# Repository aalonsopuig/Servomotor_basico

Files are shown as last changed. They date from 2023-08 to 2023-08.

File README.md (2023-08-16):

<html>

<head>
<meta http-equiv="Content-Language" content="es">
<meta name="GENERATOR" content="Microsoft FrontPage 4.0">
<meta name="ProgId" content="FrontPage.Editor.Document">
</head>

<font size="4"><b><i>Diseño de un servomotor controlado
      por bus I<sup>2</sup>C mediante microcontrolador PIC de gama media</i></b></font>
      <p>Por Alejandro Alonso Puig<br>
      Septiembre 2.003<br>
 <hr>
<p align="justify"><br>
En este repositorio podrás encontrar el código software, vídeo e informe técnico
que describe el diseño, tanto desde el punto de vista
electrónico, como informático de un modelo de servomotor basado en microcontrolador PIC16F876, cuya particularidad
consiste en ser controlado por bus I<sup>2</sup>C. Las características principales del
módulo presentado son las siguientes:&nbsp;</p>
<br>
<p align="justify">1. Actúa como Slave permitiendo seleccionar mediante
switches dip la dirección que utilizará en la red I<sup>2</sup>C.&nbsp;</p>
<p align="justify">2. Se puede establecer mediante bus I<sup>2</sup>C tanto la posición
deseada, como el DeadBand&nbsp;</p>
<p align="justify">3. Se puede obtener en todo instante mediante bus I<sup>2</sup>C
el
valor del consumo de corriente del módulo, la temperatura, la posición actual
del eje así como otros ciertos valores de estado&nbsp;</p>
<p align="justify">4. El módulo está protegido para evitar sobrecalentamiento
del mismo mediante sensor de temperatura que activa un mecanismo de ventilación
e incluso la parada del servomotor para evitar daños internos.&nbsp;</p>
<br>
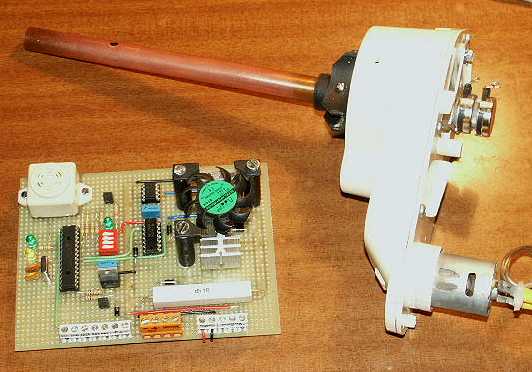
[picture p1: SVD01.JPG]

<p align="justify">La ventaja que se obtiene con este tipo de módulos es
precisamente un control completo por bus I<sup>2</sup>C que hace innecesario tener módulos
específicos para control de servos como ocurre con los de control tipo PWM. De
esta manera pueden controlarse gran cantidad de servos desde un controlador
principal sin apenas sobrecarga en el mismo. Adicionalmente se tienen medida no
habituales, como la de posición real, que permite a nivel de microcontrolador
principal, saber si el servo llegó realmente a su destino o encontró algún
obstáculo que ejercía mayor fuerza que su par. Igualmente la medida de consumo
eléctrico permite conocer cuando el servomotor tiene una sobrecarga de fuerza
contraria a su dirección de movimiento, lo que provoca una subida del consumo
eléctrico medible en este caso.</p>
<br>
<p align="justify">NOTA de 2023: Acabo de subir este proyecto antiguo (de 2003) 
que desarrollé en ensamblador, en mis inicios de aprendizaje de control, por lo que
no aplica un control en bucle cerrado decente, tipo PD o PID.</p>
<br>
<ul>
  <li>
    <p align="justify"><a href="Svd01_docum.pdf">Informe Técnico</a>    <font size="1">(.PDF
    1'9Mb)</font></li>
  <li>
    <p align="justify"><a href="SVD01_04_slave.ASM">Firmware (Programa Slave)</a> <font size="1">(.ASM
    27Kb)</font></li>
  <li>
    <p align="justify"><a href="MSVD04_master.ASM">Programa Master de ejemplo</a> <font size="1">(.ASM
    20Kb)</font></li>
  <li>
    <p align="justify"><a href="SVD01_video.AVI">Video del servo en acción</a><font size="2">
    </font><font size="1">(.AVI 2Mb)</font></li>
</ul>
<br>
<p><b>Nota</b>: Master y Slave han de estar conectados mediante tres hilos:
Masa, SCL y SDA. El módulo presentado incluye las resistencias de PullUp, por
lo que no es necesario añadirlas.&nbsp;</p>
<p>
 
<hr>

</body>

</html>

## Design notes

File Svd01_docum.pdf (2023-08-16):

mundobot.com | Alejandro Alonso Puig

# Diseño de un servomotor controlado por bus I²

C

# mediante un microcontrolador de gama media

# Alejandro Alonso Puig – mundobot.com Septiembre 2003

## Comandos I²

1

mundobot.com | Alejandro Alonso Puig

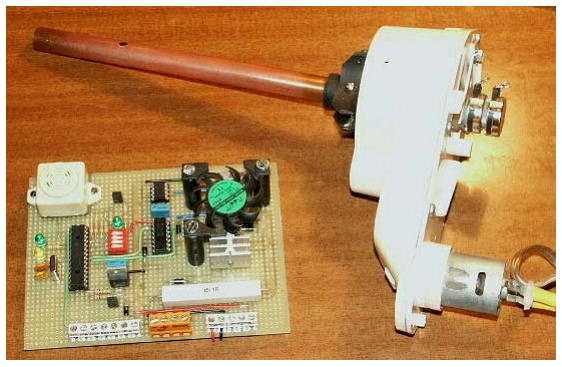
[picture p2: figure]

# Introducción

Este siguiente informe técnico describe el diseño,

## tanto desde el punto de vista electrónico, como informático de un modelo de servomotor cuya particularidad consiste en ser controlado por bus

I

2
C.

## Las características principales del módulo presentado son las siguientes:

## - Actúa como Slave permitiendo seleccionar mediante switches dip la dirección que utilizará en la red I²

C.

## - Se puede establecer mediante bus I²

C

tanto la posición deseada, como el DeadBand - Se puede obtener en todo instante mediante bus I² C el valor del consumo de corriente del módulo, la temperatura, la posición actual del eje así como otros ciertos valores de estado - El módulo está protegido para evitar sobrecalentamiento del mismo mediante sensor de temperatura que activa un mecanismo de ventilación e incluso la parada del servomotor para evitar daños

internos.

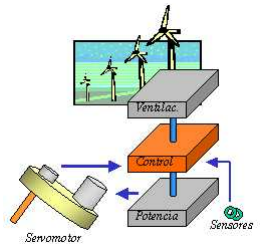
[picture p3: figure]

La ventaja que se obtiene con este tipo de módulos es precisamente un control completo por bus I² C que hace innecesario tener módulos específicos para control de servos como ocurre con los de control tipo PWM. De esta manera pueden controlarse gran cantidad de servos desde un controlador principal sin apenas sobrecarga en el mismo. Adicionalmente se tienen medida no habituales, como la de posición real, que permite a nivel de microcontrolador principal, saber si el servo llegó realmente a su destino o encontró algún obstáculo que ejercía mayor fuerza que su par. Igualmente la medida de consumo eléctrico permite conocer cuando el servomotor tiene una sobrecarga de fuerza contraria a su dirección de movimiento, lo que provoca una subida del

consumo eléctrico medible en este caso.

# Diseño Electrónico

## El módulo está básicamente compuesto por:

## - Servomotor - Sección de control - Sección de potencia para el servomotor - Sección de ventilación - Sensores - Alimentación

2

# Servomotor

## La reductora como es bien sabido permite una reducción de la velocidad de giro del eje a favor

de un aumento del par del mismo.

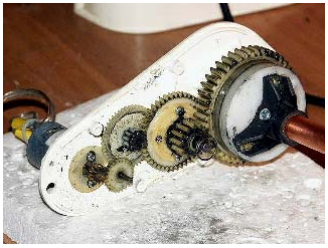
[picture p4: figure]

## En la parte trasera del eje se ha adaptado un potenciómetro lineal de 10KΩ utilizado como divisor de tensión entre 0 y 5v. La salida del

mismo irá a una entrada del microcontrolador,

## configurada para hacer una conversión analógico-digital de 8 bits de resolución, lo que implica que

se | podrán | establecer | 256 | puntos | de
posicionamiento en el servo.

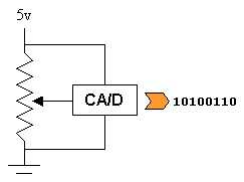
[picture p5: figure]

## El eje de la reductora se ha provisto de topes físicos para evitar que un giro incontrolado pueda

dañar los topes del potenciómetro.

# Sección de control

## La sección de control está basada en un microcontrolador PIC 16F876 de Microchip

funcionando a 4Mhz.

## Este microcontrolador posee un módulo MSSP que permite el control de las comunicaciones I²

C

## por Hardware. Se utilizan los pines SCL (RC3) y SDA (RC4) conectados a resistencias Pull-Up de 1KΩ para las comunicaciones I²

C.

Adicionalmente posee un grupo de conversores analógico digitales (A/D) de los que se utilizarán tres. Uno (RA0/AN0) para la identificación del feedback del potenciómetro, que servirá para obtener la posición del eje del servomotor; otro (RA3/AN3) para convertir la señal analógica lineal (10mV/ºC) proveniente de un sensor de temperatura (LM35), que permitirá prevenir

sobrecalentamientos | del | módulo; | y | otro

## (RA1/AN1) para medir la caída de tensión en una resistencia cementada de 1Ω colocada en serie con la alimentación del módulo de potencia, lo que permitirá identificar el consumo de corriente

del mismo y del servomotor.

## Se utilizan adicionalmente 2 salidas para la

señalización de alarmas por sobrecalentamiento.

Una (RA2) activará la sección de ventilación e indicará su actividad mediante un led. La otra (RA5) se activará solo cuando la actividad del servomotor haya sido detenida por programa debido a un sobrecalentamiento excesivo. Esta salida tiene asociado un led y está conectada a un driver que permite soportar una carga de 2 amperios. Por una parte se le conecta un buzzer de alarma, pero por otra parte se dejan salidas (X3 en esquema) para poder conectarle sistemas adicionales de acción que no superen los 2

amperios mencionados.

## Existen 4 entradas (RB2-RB5) conectadas a un switch-dip cuádruple. Solo las dos inferiores (RB2, RB3) son utilizadas por el firmware actual (versión 4) y permitirán seleccionar diferentes direcciones I² C para evitar coincidencia de

## direccionamiento con otros dispositivos (entre

01111000 [0x78] y 01111110 [0x7E]).

## Dos de las salidas (RB0 y RB1) se utilizarán para el control del servomotor. Para limpiar dichas señales de ruidos indeseados, se han filtrado a través de dobles inversores Schmith Trigger

(74LS14)

## Finalmente los pines MCLR, RB6 y RB7 se han llevado a un conector triple externo (X1 en esquema) con el fin de permitir la programación del chip una vez montado en placa. Un jumper (JP3 en esquema) permite desconectar MCLR de la resistencia de PullUp en el momento de la programación

# Sección de potencia

La sección de potencia permitirá dar al servomotor la corriente que requiere para su funcionamiento. Para ello se han utilizado sendos drivers TC4422 de Microchip que permiten consumos pico de hasta 9 amperios. Dichos drivers están protegidos de las corrientes de autoinducción del motor por un puente de 4

diodos (1N4007).

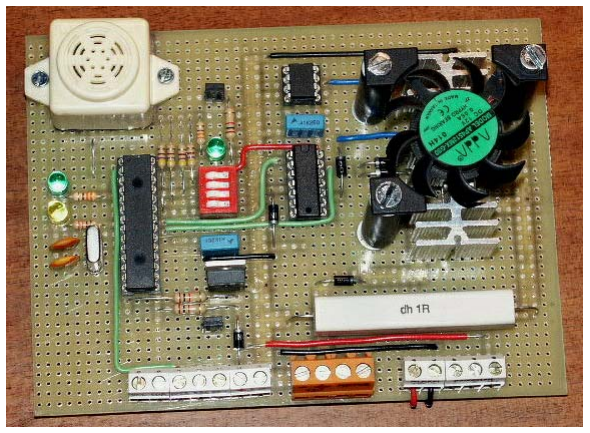
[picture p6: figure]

## Es importante tener en cuenta que la masa utilizada por la sección de potencia es diferente a la masa utilizada por el resto de las secciones. La

## razón es que ambas masas están separadas por la resistencia cementada de 1Ω que nos permite

medir el consumo de corriente del servomotor.

## Por ello existe una pequeña diferencia de potencial correspondiente a la caída de tensión en esta resistencia. Debido a esto y para evitar corrientes inversas de los drivers hacia la sección de control en los flancos de bajada, se utilizan dos

diodos (1N4007) de protección.

# Sección de ventilación

Para proteger el sistema de sobrecalentamientos,

## existe una sección de ventilación activada por la

sección de control.

Básicamente el sistema está formado por un pequeño ventilador y el driver TC4425 de Microchip. Cuando la sección de control identifica que la temperatura ha superado los 46ºC, activa RA2. Su señal es filtrada por una puerta inversora Schmith Trigger y llevada al driver mencionado. Dicho driver activa el

ventilador.

## Una vez que la sección de control considera que la temperatura ha bajado a límites adecuados

(<40ºC), detiene el ventilador.

## Cuando la temperatura sube en exceso (54º), la sección de control detendrá el servomotor, pero la sección de ventilación seguirá activa a la vez que

se activa la alarma.

# Sensores

## El sistema utiliza básicamente dos sensores:

## Sensor de temperatura (LM35): Este sensor produce una variación de potencial en su salida de 10mV por grado centígrado. En la forma en que

## se ha colocado en el circuito, permite un rango de medida de +2ºC hasta 150ºC, aunque existen otras configuraciones que permiten medidas de –55ºC hasta 150ºC (Consultar hoja técnica del fabricante

para más detalles).

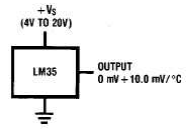
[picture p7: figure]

## Este sensor está unido al radiador de los drivers de potencia del servomotor. Por tanto solo mide la temperatura de dichos drivers y no del servomotor

u otros componentes de la circuitería.

## Sensor de corriente: En realidad no es más que la resistencia de 1Ω que se ha comentado anteriormente. Esta resistencia separa la masa de la sección de potencia y servomotor de la del resto del sistema. Es una resistencia cementada resistente al sobrecalentamiento en caso de alto

consumo de corriente por parte del servomotor.

## Como sabemos por la ley de ohm, la caída de tensión en una resistencia es directamente

proporcional a la corriente que circula por ella. (V=IxR). Si además la resistencia es de 1Ω,

V=Ix1=I, es decir que el valor de caída de potencial es idéntico a la corriente que circula por la resistencia, e igual a la corriente que circula por el servomotor (menos una pequeña corriente consumida en el driver). La realidad es que es difícil una precisión perfecta en las resistencias para que sean de 1Ω exacto, pero en cualquier caso el sistema nos resulta igualmente válido siempre que midamos previamente al montaje el valor de la resistencia y lo consideremos en la fórmula de ohm para un conocimiento exacto de

la corriente circulante.

## La masa de la sección de control y la sección de potencia están separadas por esta resistencia, por lo que la entrada al conversor A/D será

precisamente la masa de la sección de potencia, que variará según la corriente circulante.

## Al utilizar una resistencia de 1Ω, la corriente máxima circulante puede ser de 5 amperios. Si supera este valor se produciría una caída de potencial superior a 5v que al entre en el

conversor A/D podría dañar la sección de control.

## Por eso, aunque el tipo de motor utilizado tiene un consumo de 1 amperio en estado de bloqueo, es conveniente instalar un fusible de 4-5 amperios entre el polo negativo de la fuente de

alimentación y la masa de la circuitería.

## Potenciómetro: Como ya se ha comentado con anterioridad, el potenciómetro es utilizado como divisor de tensión para que permita medir la

posición del eje del servomotor en cada momento.

# Sección de Alimentación

El circuito diseñado permite utilizar dos fuentes de alimentación, de 5v y 12v. La masa de ambas fuentes de alimentación será común para obtener las mismas referencias. La fuente correspondiente a 12v alimentará el servomotor, la sección de potencia y la de ventilación, mientras que la de 5v alimentará la sección de control, el sensor de temperatura y el potenciómetro (divisor de tensión) del servomotor. Es costumbre habitual separar las fuentes de alimentación de las áreas de potencia y control para evitar que las variaciones provocadas por las áreas de potencia afecten a las áreas de control. En cualquier caso este circuito

incluye | la | posibilidad | de | alimentarlo

## exclusivamente con una fuente de alimentación de 12v. Para ello se ha dispuesto un jumper (JP1 en esquema) que permite o no obtener los 5 v necesarios a través de un regulador de tensión 7805. En las pruebas realizadas no se han percibido ruidos de importancia en la circuitería

de control.

## A continuación se muestra un esquema por bloques del sistema descrito. Las líneas de trazado

discontinuo indican las líneas de alimentación.

## Como se observará hay una línea negra más

## gruesa que las demás. Esta indica el otro plano de masas diferente al común y que es utilizado por lo

unidad de potencia.

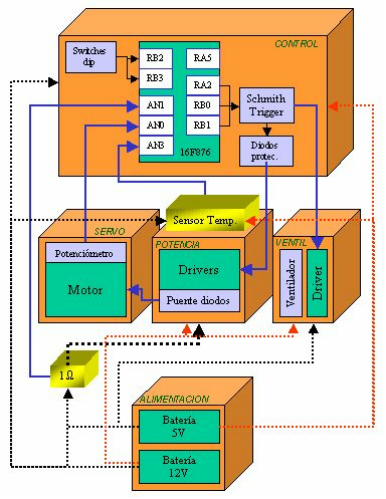
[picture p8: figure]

El esquema eléctrico completo se muestra a continuación.

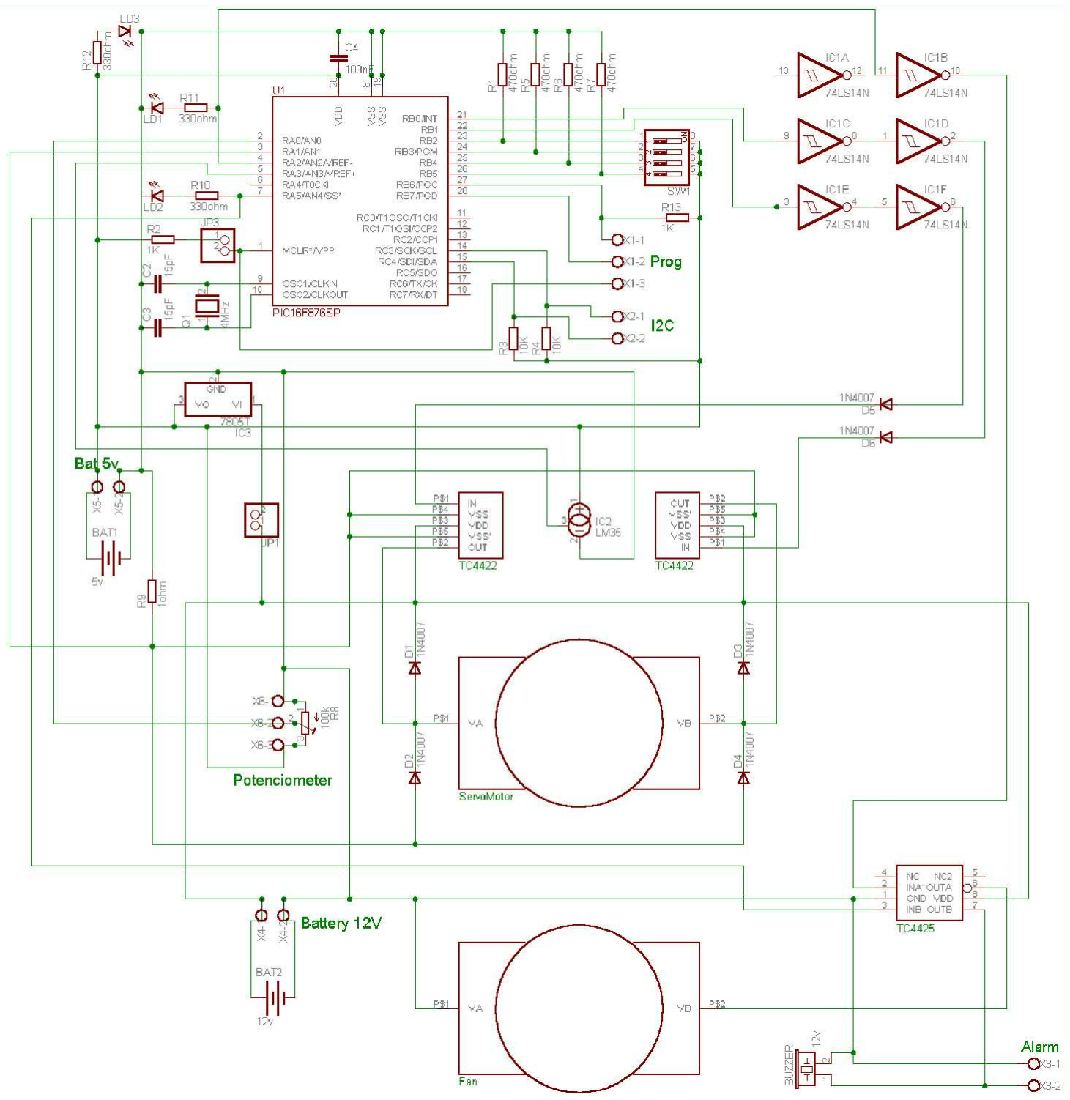
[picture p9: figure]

# Diseño del software

## El software ha sido desarrollado en ensamblador

para PIC16F876.

## El módulo está configurado para producir una interrupción cada vez que se produce un evento

I

2

## C. Al atender dicha interrupción comprueba la información que le llega al microcontrolador y

procede en consecuencia.

# Registros

## El módulo contiene una serie de registros que pueden ser accedidos desde un master por I²

C.
Algunos de estos registros son solo de lectura,

## mientras que otros son de lectura y escritura. Caso especial es uno de los registros, denominado “Estado”, que tiene algunos bits que solo son de lectura y otros que son de lectura/escritura (R/W)

## Mediante el manejo de estos registros se obtiene toda la funcionalidad del módulo. A continuación describimos dichos registros:

## - PosAct y PosNew: En realidad son accedidos desde el master como un único registro. Cuando es accedido en modo escritura, el dato se escribe sobre PosNew y cuando es accedido como lectura, el dato

devuelto es el contenido de PosAct.

## PosNew indica la posición que se desea que tenga el eje del servomotor, mientras que PosAct indica la posición real del eje en el instante en que es accedido el registro. El rango de valores aceptables para el posicionamiento del eje está entre

0+HalfDeadBand+1 y 255-HalfDeadBand-1,

## no obstante, en caso de solicitar una posición fuera de este rango, el programa forzará la posición a los límites indicados

para evitar comportamientos incorrectos.

## Esto implica que en todo momento se podrán seleccionar

### (255-HalfDeadBand-1) - (0+HalfDeadBand+1) +1

es decir,

254-2xHalfDeadBand posiciones.

## La posición por defecto que mantendrá el módulo al arrancar será la que tenga en ese momento, no variándola hasta que le llegue tal orden por I²

C.

- HalfDeadBand: Es un registro R/W.

## Indica la mitad del tamaño de la banda muerta (DeadBand), que es una franja de error aceptable en el posicionamiento del eje del servomotor. Sin esta franja el

servomotor | estaría | constantemente

## tratando de posicionarse en el lugar exacto, impidiéndoselo la inercia del motor. El rango de valores válidos está entre 0 y 255. El valor por defecto que utilizará el módulo si no se le indica otro

será 3.

- Corriente: Es un registro accedido solo en modo lectura. Permite calcular el consumo de corriente de la sección de potencia y servomotor. La medida considerada en realidad en este registro en la caída de potencial en la resistencia de 1Ω mencionada en la sección de Diseño Electrónico. La resolución tomada por el conversor A/D es de 19,5mV/bit. Es decir que por ejemplo, un valor de este registro de 37, implicaría una caída de tensión en

la resistencia de 37x19,5mV= 721,5mV.

## Es importante conocer el valor real de la resistencia si se desea tener valores precisos de consumo. Si la resistencia realmente tiene 1Ω, el consumo será de 721,5mA, pero si el valor real de la resistencia es por ejemplo de 1,5Ω, el valor de consumo de corriente según la ley

## de ohm será I = V/R = 721,5mV/1,5Ω =

481mA

## - Temperatura: Es un registro de solo lectura. Indica la temperatura de la sección de potencia del servomotor. Es utilizada internamente para la activación del sistema de ventilación o bloqueo de la unidad en caso de sobrecalentamiento. La resolución usada en la conversión A/D es

de | 5mV/bit, | que | según | las

## especificaciones del sensor lineal de temperatura utilizado corresponde a 1/2 grado/bit. Ha de tenerse en cuenta adicionalmente que la configuración establecida para el sensor hace que su

rango de valores esté entre 2ºC y 150ºC,

## por lo que una medición de 0v corresponde a 2ºC. Así un valor en este registro de por ejemplo 37 corresponde con un valor en grados centígrados de ºC = (Temperatura/2)+2 = (37/2)+2 = 20,5º

## - Estado: Se trata de un registro especial en el que el bit de mayor peso es R/W y el resto son solo de lectura. Los valores de los bits son los siguientes:

## - Bit 0: Ventilador On/Off. Solo

| lectura.

## - Bit 1: servomotor detenido por

exceso de temperatura On/Off.
| Solo lectura.

## - Bits 2 y 3: Estado posicionamiento servo. Si ambos On, está

| posicionado. | Si | solo | uno

## encendido indica que aún no está

posicionado y el sentido de giro .
| Solo lectura.

## - Bits 4, 5 y 6: No usados - Bit 7: Indica si el servomotor ha sido detenido por orden I² C. Tipo

| R/W
- Versión: Indica la versión del firmware. Es un registro de solo lectura.

# Cuerpo del programa

Básicamente el funcionamiento del programa consiste en un bucle en el que mientras le llega un comando I² C, trata de mantener el eje del servomotor en la posición indicada por “PosNew”, a la vez que actualiza los valores de los demás registros. Inicialmente “PosNew” tendrá el mismo valor que “PosAct”, por lo que si no se le indica por I² C que varíe su posición, se mantendrá de forma activa en la posición que

estaba.

## El chequeo del valor del sensor de temperatura y consiguiente actualización de su registro asociado, se hace junto con un control de márgenes de temperatura según se muestra a continuación:

## - Si el sensor indica un valor de temperatura superior a 46ºC, se activa la sección de ventilación hasta que baje de 40ºC. (RA2 activado). El sistema sigue funcionando

normalmente.

- Si el sensor indica un valor de temperatura superior a 54ºC, se detiene la sección de potencia y por tanto el servomotor hasta que baje de 40ºC. Esto se hace para proteger la unidad de daños críticos. (RA2 y RA5 activados. Este último indica estado de alarma y puede ser utilizado para activar sistemas de aviso). La sección de ventilación y la actualización de los valores de registro sigue activa, así como las funcionalidades del bus I²

C.

# Comandos I²

C

## Básicamente las órdenes que llegarán del Master al Slave serán de lectura y escritura en los registros mencionados anteriormente. En la primera transmisión se indica el número de registro al que se quiere acceder, bien sea para

## lectura o escritura. Dicha numeración es la siguiente:

1. Registro de Estado.
2. No usado.

## 3. Posición. En lectura "PosAct" en escritura "PosNew" 4. Temperatura 5. Corriente 6. HalfDeadBand

7. Revisión Firmware.

## A continuación se muestra el formato de los comandos I² C utilizados para el intercambio de datos entre Master y Slave a nivel de lógica

digital.

## Escritura registro

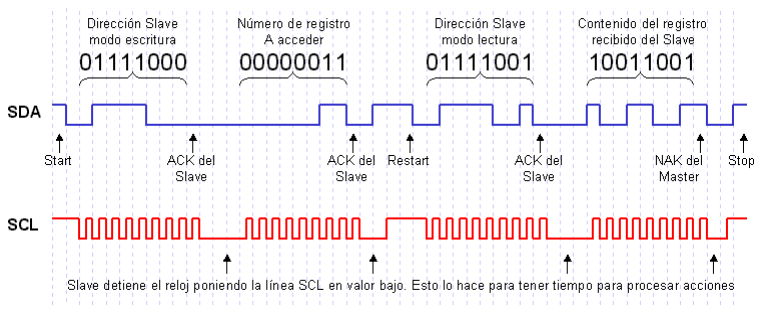
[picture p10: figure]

## El Master envía tres bytes. El primero contiene la dirección del Slave. El segundo, el número de registro a actualizar. El tercero, el dato a escribir

en el registro.

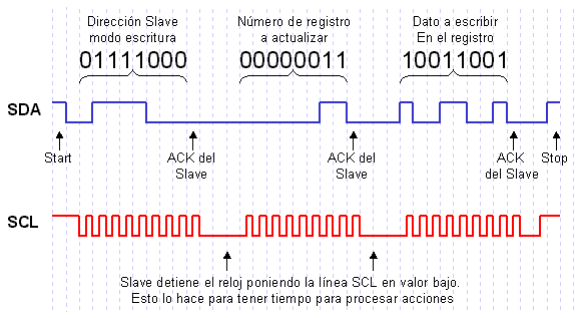
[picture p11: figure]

## Lectura Registro

## Se hacen dos transferencias de dos bytes cada uno. En la primera el Master envía la dirección del Slave y el número de registro a leer. En la segunda transmisión el Master envía la dirección del Slave (pero con bit de lectura) y el Slave envía

el contenido del registro escogido.

# Código fuente

A continuación se incluye el código fuente del servomotor, que actúa tal como se ha comentado en modo Slave.

; SVD01_04
;
; Programa servocontrol (Slave) ; Por: Alejandro Alonso Puig
; Fecha: 10/9/2003
; Controlador: 16F876
; Función:
; Permite control en bucle cerrado de la posición de un motoreductor con ; entrada de feedback por potenciometro. Básicamente es el programa que ; consigue el funcionamiento como servomotor.
; La comunicación con el exterior se hace mediante bus I2C.
; Adicionalmente se mide el consumo de corriente y temperatura
; Tiene medidas de autoprotección con activación de una señal para ventilación ; en caso de superar una temperatura dada y parada de servomotor en caso de
; superar una temperatura límite.
; Shitches dip para especificar la dirección i2c que se utilizará

list | p=16F876
include | "P16F876.INC"

;Definición de macros

#define Ventilador | PORTA,2 ;Bit de activación de ventilador

#define AlarmaTemp | PORTA,5 ;Bit de activación de alarma. El módulo se detiene

| | ;por exceso de temperatura.
#define Version | d'04' | ;Versión del programa

;Definición de variables

cblock 0x20

HalfDeadBand ;valor de mitad de banda de precisión de posicionamiento ;cuanto menor sea, más precisa es la posición ;DeadBand=2*HalfDeadBand
PosAct | ;Posición actual del servo según Potenciómetro (0 a 255)
PosNew | ;Posicion deseada del servo (0+HalfDeadBand+1 a 255-HalfDeadBand-1)
PosNewL | ;PosNewL y PosNewH son los extremos inferior y superior..
PosNewH | ;..a PosNew para establecer el margen según "DeadBand"
PosMax | ;Valores máximo y mínimo que se puede dar a "PosAct"...
PosMin | ;..en función del HalfDeadBand. Básicamente son..
;(0+HalfDeadBand+1 a 255-HalfDeadBand-1)
Corriente | ;Consumo de corriente del módulo (ver proc ChkCurrent)
Temperatura | ;Temperatura del módulo de potencia (ver proc ChkTemperatura)
Estado | ;Registro especial de estado del módulo
; | Bit0: Ventilador On/Off
; | Bit1: servomotor detenido por exceso de temperatura On/Off
; | Bits2 y 3: Estado posicionamiento servo. Si ambos On, está
; | posicionado. Si solo uno encendido indica que aún
; | no está posicionado y el sentido de giro.
; | Bit7: Indica si el servomotor ha sido detenido por orden i2c
DirNodo | ;Dirección I2C de este slave (4 posibles direcciones segun switches dip)
MensajeIn | ;Contendrá el dato recibido por I2C del master
MensajeOut | ;Contendrá el dato a enviar por I2C al master
BkStatus | ;Backup del registro STATUS
BkW | ;Backup W
Temp | ;Variable Temporal usada para evaluación de eventos I2C
Registro | ;Registro accedido por i2c:
; | 1: Registro de Estado. Variable "Estado"
; | 2: No usado. Reservado para velocidad en proximas versiones
; | 3: Posición. En lectura "PosAct" en escritura "PosNew"
; | 4: Temperatura
; | 5: Corriente
; | 6: HalfDeadBand
; | 7: Revisión Firmware. "Version"
StatI2C | ;Registro intermedio para identificar el estado i2c:
; | 0: Si On --> llegó dato Registro (por tanto si llega llega otro
; | dato, será para sobreescribir contenido registro dado)
BDel0 | ;Usada en retardos
BDel1 | ;Usada en retardos
BDel2 | ;Usada en retardos
Pausa | ;Usada para hacer pausas con subr "HacerTiempo"
endc | ;Fin de definiciones
org | 0
goto | INICIO
org | 5

;-------------------------------------------------------------------------------
Interrupcion | ;RUTINA DE INTERRUPCIÓN. Se ocupa de los eventos I2C
;-------------------------------------------------------------------------------

;Guardamos copia de algunos registros

movwf | BkW | ;Hace copia de W
movf | STATUS,W | ;Hace copia de registro de estado
banksel PORTA
movwf BkStatus

;Chequeamos si la interrupción es por evento I2C. En caso positivo llamamos ;a la rutina de proceso del evento
banksel PIR1
btfss | PIR1,SSPIF | ;Ha ocurrido un evento SSP? (I2C)
goto | IntNoSSP | ;No. entonces será por otra cosa. Saltamos.
call | SSP_Handler | ;Si. Procesamos el evento. Si se reciben ordenes, quedarán
| | ;registradas en "MensajeIn". Se enviarán las ordenes
| | ;guardadas en "MensajeOut".
banksel PIR1
bcf | PIR1,SSPIF | ;Limpiamos el flag
goto | Rest
IntNoSSP | ;Aquí se gestionan interrupciones que no son por SSP
; |
; En caso de necesitarse, poner aquí la rutina de gestión de interrupciones ; que no sean por bus I2C
; |
Rest | ;Restauramos las copias de los registros
movf | BkStatus,W | ;Restaura las copias de registros
movwf | STATUS | ;registro de estado
movf | BkW,W | ;registro W

retfie

;-------------------------------------------------------------------------------

INICIO | ;Inicio del cuerpo del programa
banksel TRISB | ;Apunta a banco 1
movlw | b'00111100' | ;Salida excepto B2, B3, B4 y B5 que tiene switches dip
movwf | TRISB | ;

;Configuración para uso de conversor A/D
banksel ADCON1
movlw | b'00001011' | ;Establece puerta A como salida excepto RA0 ...
movwf | TRISA | ;..(Potenciómetro), RA1 (medición corriente) y RA3 (Temperatura)
movlw | b'00000100' | ;PORTA: RA0, RA1, RA3 entrada analog. Resto dig. Justif ADRESH
movwf | ADCON1 | ;

;Inicialización variable de posición del servomotor
banksel PosAct
call | ChkPosAct | ;Identificación posición actual del servo..
movf | PosAct,W | ;..y la guardamos en PosNew..
movwf | PosNew | ;..para que el servo no se mueva...

;Establecemos valor de DeadBand por defecto. Se puede modificar por i2c
movlw | d'3'
movwf | HalfDeadBand

;Establecemos valor registro especial de estado por defecto
movlw | b'10000000'
movwf | Estado

;Configuración para gestión i2c
call init_i2c_Slave ;Configuración para uso de i2c banksel INTCON
bsf | INTCON,GIE | ;Activamos las interrupciones

banksel PORTA
clrf | PORTA
clrf | PORTB
clrf | StatI2C

BUCLE | ;Bucle principal del programa
StSt | ;Chequeo bit de start/stop del servomotor en registro especial de estado
btfsc | Estado,7 | ;On:servomotor funciona, Off:servomotor se detiene
goto | StON | ;Está On. Seguimos
call | PararMotor | ;Está Off. Paramos servomotor,...
call | ChkPosAct | ;..pero seguimos midiendo variables...
call | ChkCurrent | ;..por si son solicitadas por i2c
call | ChkTemperatura ;Además el ventilador seguira activo si es necesario
goto | StSt | ;y nos mantenemos en bucle hasta que se active por i2c

StON

;Chequeo Temperatura
call ChkTemperatura

;Chequeo de consumo eléctrico
call ChkCurrent

;Verificamos valor de PosNew para que no sobrepase los límites: ;(0+HalfDeadBand+1 a 255-HalfDeadBand-1)
;Si PosNew > 255-HalfDeadBand-1 then PosNew=255-HalfDeadBand-1 ;Si PosNew < HalfDeadBand+1 then PosNew=HalfDeadBand+1
movf | HalfDeadBand,W
addlw | d'1'
movwf | PosMin | ;0+HalfDeadBand+1
movlw | d'254'
movwf | PosMax
movf | HalfDeadBand,W
subwf | PosMax,F | ;255-HalfDeadBand-1

;Checkea si PosNew > PosMax
movf | PosMax,W | ;
subwf | PosNew,W | ;Resta/compara con "PosNew"
btfsc | STATUS,Z | ;Son iguales (Z=1)??
goto | OkSigue | ;Si. Está en el límite de posición, pero es correcto
btfsc | STATUS,C | ;No. Mayor (C=0)??
goto | FuerzaMax | ;Si. (PosNew > PosMax) Forzamos que no pase del límite
goto | ChkMenos | ;No, (PosNew < PosMax)
ChkMenos | ;Checkea si PosNew < PosMin
movf | PosMin,W | ;
subwf | PosNew,W | ;Resta/compara con "PosNew"
btfsc | STATUS,Z | ;Son iguales (Z=1)??
goto | OkSigue | ;Si. Está en el límite de posición, pero es correcto
btfsc | STATUS,C | ;No. Mayor (C=0)??
goto | OkSigue | ;Si. (PosNew > PosMin) está ok: PosMin<PosNew<PosMax
goto | FuerzaMin | ;No, (PosNew < PosMin) Forzamos que no pase del límite
FuerzaMax | ;Fuerza a que la posición no pase del máximo
movf | PosMax,w
movwf | PosNew
goto | OkSigue
FuerzaMin | ;Fuerza a que la posición no pase del mínimo
movf | PosMin,W
movwf | PosNew
goto | OkSigue

OkSigue

;Cálculo PosNewH y PosNewL en función del valor de PosNew
movf | PosNew,W
movwf | PosNewH
movwf | PosNewL
movf | HalfDeadBand,W
addwf | PosNewH,F
subwf | PosNewL,F

;Identificación posición actual del servo
call | ChkPosAct
ChkMayor | ;Checkea si PosAct > PosNewH --> Giro antihorario
movf | PosNewH,W | ;
subwf | PosAct,W | ;Resta/compara con "PosAct"

btfsc | STATUS,Z | ;Son iguales (Z=1)??
goto | OkPosic | ;Si. Está en el límite de DeadBand pero se da por bueno
btfsc | STATUS,C | ;No. Mayor (C=0)??
goto | GiroAntihora | ;Si. (PosAct > PosNewH) Activamos motor
goto | ChkMenor | ;No, (PosAct < PosNewH)
ChkMenor | ;Checkea si PosAct < PosNewL --> Giro antihorario
movf | PosNewL,W | ;
subwf | PosAct,W | ;Resta/compara con "PosAct"
btfsc | STATUS,Z | ;Son iguales (Z=1)??
goto | OkPosic | ;Si. Está en el límite de DeadBand pero se da por bueno
btfsc | STATUS,C | ;No. Mayor (C=0)??
goto | OkPosic | ;Si. (PosAct > PosNewL) está en Deadband:PosNewL< PosAct < PosNewH
goto | GiroHora | ;No, (PosAct < PosNewL) Activamos motor
OkPosic | ;Paramos motor
call | PararMotor
goto | BUCLE
GiroHora | ;Activamos motor sentido Horario y actualizamos valor registro especial Estado
bsf | PORTB,0
bcf | PORTB,1
bsf | Estado,2
bcf | Estado,3
goto | BUCLE
GiroAntihora | ;Activamos motor sentido Antihorario y actualizamos valor registro especial Estado
bcf | PORTB,0
bsf | PORTB,1
bcf | Estado,2
bsf | Estado,3
goto | BUCLE
goto | BUCLE

;********************************************************************************* ; SUBRUTINAS
;*********************************************************************************

;-------------------------------------------------------------------------------
ChkPosAct | ;Identifica la posición actual del servo mediante la
;la conversión A/D del valor dado por el potenciómetro ;y lo deja en la variable "PosAct" ;-------------------------------------------------------------------------------

;Tomaremos datos de ADRESH
banksel ADCON1
bcf ADCON1,ADFM

banksel ADCON0
movlw | b'11000001' | ;PORTA-RA0: osci interno, canal-0, activar captura
movwf | ADCON0 | ;
movlw | d'1' | ;Pausa para que de tiempo al condensador interno...
movwf | Pausa | ;..a capturar el valor analógico
call | HacerTiempo
bsf | ADCON0,GO | ;Comenzar conversión A/D
AD_W1 | btfsc | ADCON0,GO_DONE ;Conversión finalizada?
goto | AD_W1
movf | ADRESH,W
movwf | PosAct | ;Guarda en variable de posición actual
return

;-------------------------------------------------------------------------------
ChkCurrent | ;Obtiene el consumo de corriente del módulo servomotor
;mediante conversión A/D de la caida de potencial de una ;resistencia de 1 ohm. El valor obtenido se almacena en la ;variable "Corriente" de manera que el consumo en amperios

;se puede calcular con la fórmula siguiente:
; | Amperios=(Corriente x 0.02)/R
;siendo R la resistencia de medición, que en principio es de ;1ohm, pero que conviene medir para que los calculos sean exactos ;La máxima corriente que puede medir es 255x0.02=5.1 amperios ;Si la corriente va a ser superior, habra que reducir el valor ;de la resistencia de manera que Max Amperios x R < 5 ;-------------------------------------------------------------------------------

;Tomaremos datos de ADRESH
banksel ADCON1
bcf ADCON1,ADFM

banksel ADCON0
movlw | b'11001001' | ;PORTA-RA1: osci interno, canal-1, activar conversion
movwf | ADCON0 | ;
movlw | d'1' | ;Pausa para que de tiempo al condensador interno...
movwf | Pausa | ;..a capturar el valor analógico
call | HacerTiempo
bsf | ADCON0,GO | ;Comenzar conversión A/D
AD_W2 | btfsc | ADCON0,GO_DONE ;Conversión finalizada?
goto | AD_W2
movf | ADRESH,W
movwf | Corriente | ;Guarda en variable de medición de corriente
return

;-------------------------------------------------------------------------------
ChkTemperatura | ;Obtiene la temperatura del módulo de potencia del servomotor
;mediante conversión A/D de la salida del sensor LM35 ;y la almacena en la variable "Temperatura"
;La temperatura en ºC del módulo será igual a:
; | ºC=(Temperatura/2)+2
;-------------------------------------------------------------------------------

;Tomaremos datos de ADRESL para tener una precisión de medio grado por bit banksel ADCON1
bsf ADCON1,ADFM

banksel ADCON0
movlw | b'11011001' | ;PORTA-RA3: osci interno, canal-3, activar conversion
movwf | ADCON0 | ;
movlw | d'1' | ;Pausa para que de tiempo al condensador interno...
movwf | Pausa | ;..a capturar el valor analógico
call | HacerTiempo
bsf | ADCON0,GO | ;Comenzar conversión A/D
AD_W3 | btfsc | ADCON0,GO_DONE ;Conversión finalizada?
goto | AD_W3
banksel ADRESL
movf ADRESL,W
banksel Temperatura
movwf | Temperatura | ;Guarda en variable de medición de temperatura

;Los drivers utilizados tienen un rango de funcionamiento entre 0º y 70ºC ;Checkeamos si ha superado 46ºC, con lo que activaríamos ventilador hasta ;que baje de 40ºC
movlw | d'88' | ;46ºC=factor 88 --->(88/2)+2=46
subwf | Temperatura,W ;Resta/compara con "Temperatura"
btfsc | STATUS,Z | ;Son iguales (Z=1)??
goto | VentiladorOn | ;Si. Activamos ventilador
btfsc | STATUS,C | ;No. Mayor (C=0)??
goto | VentiladorOn | ;Si. Límite de temperatura superado
;No, verificamos si menor que 40º
movlw | d'76' | ;40ºC=factor 76 --->(76/2)+2=40
subwf | Temperatura,W ;Resta/compara con "Temperatura"
btfsc | STATUS,Z | ;Son iguales (Z=1)??
goto | FinChk | ;Si. no hacemos nada. Si ventilador activado, continuará así
btfsc | STATUS,C | ;No. Mayor (C=0)??
goto | FinChk | ;Si. no hacemos nada. Si ventilador activado, continuará así
goto | VentiladorOff ;No, ha bajado de 40º, podemos desactivar ventilador

VentiladorOn

bsf | Ventilador | ;Activamos ventilador
bsf | Estado,0 | ;..y registro especial de estado

;Checkeamos si ha superado 54ºC, con lo que detendríamos el módulo ;para evitar sobrecalentamiento hasta que baje de 40ºC
movlw | d'104' | ;54ºC=factor 104 --->(104/2)+2=54
subwf | Temperatura,W ;Resta/compara con "Temperatura"
btfsc | STATUS,Z | ;Son iguales (Z=1)??
goto | AlarmOn | ;Si. Activamos procedimiento de alarma por sobrecalentamiento
btfsc | STATUS,C | ;No. Mayor (C=0)??
goto | AlarmOn | ;Si. Límite de temperatura superado
;No, todo en orden
goto FinChk

VentiladorOff
bcf | Ventilador | ;Paramos ventilador
bcf | Estado,0 | ;..y registro especial de estado
goto | FinChk

AlarmOn ;Procedimiento ante sobrecalentamiento del módulo

;Paramos motor
call PararMotor

;Activamos bit de alarma por sobrecalentamiento
bsf | AlarmaTemp
bsf | Estado,1 | ;..y registro especial de estado
ChkT | ;Entramos en bucle hasta que baje de 40ºC
banksel ADCON0
movlw | b'11011001' | ;PORTA-RA3: osci interno, canal-3, activar conversion
movwf | ADCON0 | ;
movlw | d'1' | ;Pausa para que de tiempo al condensador interno...
movwf | Pausa | ;..a capturar el valor analógico
call | HacerTiempo
bsf | ADCON0,GO | ;Comenzar conversión A/D
AD_W4 | btfsc | ADCON0,GO_DONE ;Conversión finalizada?
goto | AD_W4
banksel ADRESL
movf ADRESL,W
banksel Temperatura
movwf | Temperatura | ;Guarda en variable de medición de temperatura
movlw | d'76' | ;40ºC=factor 76 --->(76/2)+2=40
subwf | Temperatura,W ;Resta/compara con "Temperatura"
btfsc | STATUS,Z | ;Son iguales (Z=1)??
goto | ChkT | ;Si. continuamos en bucle hasta que se enfrie
btfsc | STATUS,C | ;No. Mayor (C=0)??
goto | ChkT | ;Si. continuamos en bucle hasta que se enfrie
bcf | AlarmaTemp | ;No, ha bajado de 40º, podemos desactivar condicion alarma
bcf | Ventilador | ;Paramos ventilador
bcf | Estado,0 | ;..y registro especial de estado
goto | FinChk

FinChk
return

;-------------------------------------------------------------------------------
PararMotor | ;Detiene el servomotor
;-------------------------------------------------------------------------------
bsf | PORTB,0
bsf | PORTB,1
bsf | Estado,2
bsf | Estado,3
return

;-------------------------------------------------------------------------------
init_i2c_Slave | ;Inicializa valores para uso de I2C en Slave ;Ha de ser llamado tras definir TRISC (de ser necesario)

;-------------------------------------------------------------------------------

;Guardamos copia de algunos registros
movwf | BkW | ;Hace copia de W
movf | STATUS,W | ;Hace copia de registro de estado
banksel PORTA
movwf BkStatus

;Establecemos dirección del esclavo segun switches dip (B2 y B3)
movlw | b'01111000'
movwf | DirNodo
btfsc | PORTB,2
bsf | DirNodo,2
btfsc | PORTB,3
bsf | DirNodo,1

;Configuramos I2C
banksel TRISC | ; Pasamos a direccionar Banco 1
movlw | b'00011000' | ; Establece líneas SDA y SCL como entradas...
iorwf | TRISC,F | ;..respetando los valores para otras líneas.
bcf | SSPSTAT,CKE | ; Establece I2C input levels
bcf | SSPSTAT,SMP | ; Habilita slew rate
bsf | SSPCON2,GCEN | ; Habilita direccionamiento global
banksel DirNodo
movf | DirNodo,W | ; Dirección esclavo
banksel SSPADD
movwf | SSPADD | ;
banksel SSPCON | ; Pasamos a direccionar Banco 0
movlw | b'00110110' | ; Slave mode, SSP enable,
movwf | SSPCON | ;
bcf | PIR1,SSPIF | ; Limpia flag de eventos SSP
bcf | PIR1,7 | ; Limpia bit. Mandatorio por Datasheet

;Configuración para interrupciones por evento I2C
banksel PIE1
bsf | PIE1,SSPIE
bsf | INTCON,PEIE

;Restauramos las copias de los registros
movf | BkStatus,W | ;Restaura las copias de registros
movwf | STATUS | ;registro de estado
movf | BkW,W | ;registro W

return

; --------------------------------------------------------------------------------------SSP_Handler ; Este manejador controla cada evento SSP (I2C) acontecido.
; El código que se muestra abajo chequea 5 posibles estados. ; Cada uno de los 5 estados SSP son identificados haciendo
; XOR de los bits del registro SSPSTAT con mascaras de bits ; predeterminadas. Una vez que el estado ha sido identificado
; se llevan a cabo las acciones pertinentes. Los estados
; indefinidos son considerados como estados de error.

; State 1: Operación de escritura I2C, ultimo byte era de dirección. ; SSPSTAT bits: S = 1, D_A = 0, R_W = 0, BF = 1

; State 2: Operación de escritura I2C, ultimo byte era de datos.
; SSPSTAT bits: S = 1, D_A = 1, R_W = 0, BF = 1

; State 3: Operación de lectura I2C, ultimo byte era de dirección. ; SSPSTAT bits: S = 1, D_A = 0, R_W = 1, BF = 0

; State 4: Operación de lectura I2C, ultimo byte era de datos.
; SSPSTAT bits: S = 1, D_A = 1, R_W = 1, BF = 0

; State 5: Reset lógico del Slave I2C por NACK del master.
; SSPSTAT bits: S = 1, D_A = 1, R_W = 0, BF = 0

; --------------------------------------------------------------------------------------

banksel SSPSTAT
movf | SSPSTAT,W | ; Obtiene el valor de SSPSTAT
andlw | b'00101101' | ; elimina los bits no importantes SSPSTAT.

banksel Temp
movwf | Temp | ; para chequeo posterior.
State1: | ; Operación de escritura, ultimo byte ha sido
movlw | b'00001001' | ; de dirección, el buffer está lleno.
banksel Temp
xorwf | Temp,W | ;
btfss | STATUS,Z | ; Estamos en el primer estado?
goto | State2 | ; No, checkeamos siguiente estado
call | ReadI2C | ; SI. Hacemos un read SSPBUF (para vaciar buffer).
| | ; El Hardware se ocupa de mandar Ack
return
State2: | ; Operación de escritura, ultimo byte ha sido
movlw | b'00101001' | ; de datos, el buffer está lleno.
banksel Temp
xorwf | Temp,W
btfss | STATUS,Z | ; Estamos en el segundo estado?
goto | State3 | ; NO, checkeamos siguiente estado
call | ReadI2C | ; SI, Tomamos el byte del SSP.

;Aquí tenemos en W el valor del dato recibido
movwf | MensajeIn
btfsc | StatI2C,0 | ;Chequeamos si ya sabíamos el registro a actualizar y es un dato
goto | LoSabemos | ;Lo sabíamos, es un dato
movf | MensajeIn,W | ;No lo sabíamos, nos acaba de llegar
movwf | Registro
bsf | StatI2C,0
return
LoSabemos | ;Sabemos el registro y tenemos el dato, actualizamos dato del registro
call | UpdateReg
bcf | StatI2C,0 | ;Limpiamos flag
return
State3: | ; Operación de lectura, ultimo byte ha sido
movlw | b'00001100' | ; de dirección, el buffer está vacío
banksel Temp
xorwf | Temp,W
btfss | STATUS,Z | ; Estamos en el tercer estado?
goto | State4 | ; NO, checkeamos siguiente estado
| | ; SI
btfsc | StatI2C,0 | ;Chequeamos si ya sabemos el registro a leer
goto | LoSabemosR | ;Lo sabemos,
movlw | 0 | ;No lo sabemos, devolvemos un cero por defecto
call | WriteI2C | ;escribimos el byte en SSPBUF
return
LoSabemosR | ;Sabemos el registro a leer. Lo leemos y enviamos el dato
call | ReadReg
movf | MensajeOut,W
call | WriteI2C | ; SI, escribimos el byte en SSPBUF
bcf | StatI2C,0 | ; Limpiamos flag de número de registro recibido
return
State4: | ; Operación de lectura, ultimo byte ha sido
movlw | b'00101100' | ; de datos, el buffer está vacío
banksel Temp
xorwf | Temp,W
btfss | STATUS,Z | ; Estamos en el cuarto estado?
goto | State5 | ; NO, checkeamos siguiente estado
| | ; SI. Operación no admitida.
movlw | 0 | ; devolvemos un cero por defecto
call | WriteI2C | ; escribimos el byte en SSPBUF
return

State5:
movlw | b'00101000' | ; Se ha recibido un NACK mientras se transmitían...
banksel Temp
xorwf | Temp,W | ; ..datos al master. Lo lógica del Slave..
btfss | STATUS,Z | ; ..se resetea en este caso. R_W = 0, D_A = 1
goto | I2CErr | ; y BF = 0
return | | ; Si no estamos en State5, entonces es
| | ; que algo fue mal

I2CErr nop | | ; Algo fue mal
return

;---------------------------------------------------------------------
WriteI2C | ;Usada por SSP_Handler para escribir datos en bus I2C
;---------------------------------------------------------------------

banksel SSPCON
movwf | SSPBUF | ; Escribe el dato en W
bsf | SSPCON,CKP | ; Libera el reloj
return

;---------------------------------------------------------------------
ReadI2C | ;Usada por SSP_Handler para escribir datos en bus I2C
;---------------------------------------------------------------------

banksel SSPBUF
movf | SSPBUF,W | ; Toma el byte y lo guarda en W
return

;---------------------------------------------------------------------
UpdateReg | ;Actualiza Registro ordenado por I2C
;---------------------------------------------------------------------

;Procedemos a actuar según la orden recibida del Master. Haremos un Pseudo CASE ;que actualice solo los registros escribibles e ignore los que no se puedan escribir

M_01 | ;Estado
movlw | d'1' | ;
xorwf | Registro,W | ;
btfss | STATUS,Z | ; Es este el registro a actualizar?
goto | M_03 | ; No, chequeamos siguiente caso
| | ; Si. procedemos a actualizar el registro (solo bits R/W)
bsf | Estado,7 | ; Flag 7: On/Off servomotor
btfss | MensajeIn,7 | ; Simplemente establecemos el mismo valor de bit...
bcf | Estado,7 | ; ...que nos ha llegado a "MensajeIn"
return | | ;Regresamos a la espera de una nueva orden
M_03 | ;Posición. En Escritura es PosNew
movlw | d'3' | ;
xorwf | Registro,W | ;
btfss | STATUS,Z | ; Es este el registro a actualizar?
goto | M_06 | ; No, chequeamos siguiente caso
movf | MensajeIn,W | ; Si. procedemos a actualizar el registro
movwf | PosNew
return | | ;Regresamos a la espera de una nueva orden
M_06 | ;HalfDeadBand
movlw | d'6' | ;
xorwf | Registro,W | ;
btfss | STATUS,Z | ; Es este el registro a actualizar?
goto | M_Error | ; No, chequeamos siguiente caso
movf | MensajeIn,W | ; Si. procedemos a actualizar el registro
movwf | HalfDeadBand
return | | ;Regresamos a la espera de una nueva orden

M_Error ;No es un registro conocido o es de solo lectura. Se ignora.

return

;---------------------------------------------------------------------
ReadReg | ;Leemos Registro solicitado por I2C
;---------------------------------------------------------------------

;Haremos un Pseudo CASE que lea el registro solicitado y lo deje en MensajeOut

M_01R | ;Estado
movlw | d'1' | ;

xorwf | Registro,W | ;
btfss | STATUS,Z | ; Es este el registro a leer?
goto | M_03R | ; No, chequeamos siguiente caso
movf | Estado,W | ; Si. procedemos a leer el registro
movwf | MensajeOut
return | | ;Regresamos a la espera de una nueva orden
M_03R | ;Posición. En Lectura es PosAct
movlw | d'3' | ;
xorwf | Registro,W | ;
btfss | STATUS,Z | ; Es este el registro a leer?
goto | M_04R | ; No, chequeamos siguiente caso
movf | PosAct,W | ; Si. procedemos a leer el registro
movwf | MensajeOut
return | | ;Regresamos a la espera de una nueva orden
M_04R | ;Temperatura
movlw | d'4' | ;
xorwf | Registro,W | ;
btfss | STATUS,Z | ; Es este el registro a leer?
goto | M_05R | ; No, chequeamos siguiente caso
movf | Temperatura,W ; Si. procedemos a leer el registro
movwf | MensajeOut
return | | ;Regresamos a la espera de una nueva orden
M_05R | ;Corriente
movlw | d'5' | ;
xorwf | Registro,W | ;
btfss | STATUS,Z | ; Es este el registro a leer?
goto | M_06R | ; No, chequeamos siguiente caso
movf | Corriente,W | ; Si. procedemos a leer el registro
movwf | MensajeOut
return | | ;Regresamos a la espera de una nueva orden
M_06R | ;HalfDeadBand
movlw | d'6' | ;
xorwf | Registro,W | ;
btfss | STATUS,Z | ; Es este el registro a leer?
goto | M_07R | ; No, chequeamos siguiente caso
movf | HalfDeadBand,W | ; Si. procedemos a leer el registro
movwf | MensajeOut
return | | ;Regresamos a la espera de una nueva orden
M_07R | ;Version
movlw | d'7' | ;
xorwf | Registro,W | ;
btfss | STATUS,Z | ; Es este el registro a leer?
goto | M_ErrorR | ; No, chequeamos siguiente caso
movlw | Version | ; Si. procedemos a leer el registro (en este caso una constante)
movwf | MensajeOut
return | | ;Regresamos a la espera de una nueva orden
M_ErrorR | ;No es un registro conocido. Se devuelve valor 0
clrf | MensajeOut
return

;---------------------------------------------------------------------------------------HacerTiempo ;realiza una pausa del numero de centesimas de segundo especificadas en "Pausa" ;El tiempo real es aproximado, dependiendo del número de interrupciones ;que se producan.
;---------------------------------------------------------------------------------------
movf | Pausa,W | ;Coloca el valor de pausa en BDel2...
movwf | BDel2 | ;...para no alterar su contenido
; |
; Generado con PDEL ver SP r 1.0 el 24/02/03 Hs 18:31:22
; Descripcion: Delay 10000 ciclos (1 centésima de segundo)
; |
BCiclo movlw | .8 | ; 1 set numero de repeticion (B)
movwf | BDel0 | ; 1 |
BLoop1 movlw | .249 | ; 1 set numero de repeticion (A)
movwf | BDel1 | ; 1 |
BLoop2 nop | | ; 1 nop

nop | | ; 1 ciclo delay
decfsz | BDel1, 1 ; 1 + (1) es el tiempo 0 ? (A)
goto | BLoop2 | ; 2 no, loop
decfsz | BDel0, 1 ; 1 + (1) es el tiempo 0 ? (B)
goto | BLoop1 | ; 2 no, loop
BDelL1 goto BDelL2 | ; 2 ciclos delay
BDelL2 nop | | ; 1 ciclo delay
; |
decfsz BDel2,F | ;Repite tantas veces el ciclo de una decima de segundo...
goto | BCiclo | ;..como se lo indique BDel2
return | | ; 2+2 Fin.

Fin
END

# Ejemplo de Master

El siguiente sería un ejemplo de montaje electrónico para el Master que controlaría dicho servomotor.

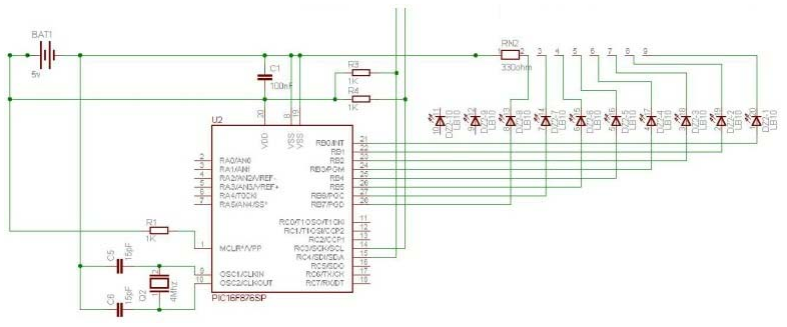
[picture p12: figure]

A continuación se incluye un ejemplo de código para el Master, que hace que el servo se mueva de un extremo a otro con una pausa de unos 2 segundos entre cambios de posición. Asimismo solicita al servomotor (Slave) el dato de consumo de corriente y lo muestra por los leds conectados al puerto B. El código para controlar el Servo ha de incluirse en el cuerpo del programa (donde el bucle MLoop).

; MSVD04
; Master para control Servo SVD01_04 ; Por: Alejandro Alonso Puig
; Fecha: 10/9/2003
; Controlador: 16F876
; Función:
; Controla por I2C el módulo servomotor SVD01 v4
; Como ejemplo, mueve el servomotor de un lado al otro y va mostrando el valor del ; registro de consumo de corriente por barrera de leds conectada
; al puerto B
;
; Las subrutinas definidas para el intercambio de datos con el módulo SVD01 (Servomotor) ; son los siguientes:
;

; LECTURA DE REGISTROS
; --------------------
;
; ReadPosSVD01 | Obtiene por i2c la posición del módulo de servomotor
; | y la deja en la variable "PosActSVD01"
; ReadTempSVD01 | Lee el valor de temperatura del módulo SVD01 y la deja
; | en "TempSVD01"
; ReadCurrSVD01 | Lee el valor de consumo del módulo SVD01
; | y lo deja en la variables "CurrSVD01"
; ReadStatSVD01 | Lee el registro de estado del módulo SVD01 y lo deja
; | en "StatSVD01"
; ReadHDBSVD01 | Obtiene por i2c el registro HalfDeadBand del módulo de
; | servomotor y la deja en la variable "HDBSVD01"
; ReadVerSVD01 | Obtiene por i2c la versión de firmware del módulo de
; | servomotor y la deja en la variable "VerSVD01"
;
; ESCRITURA DE REGISTROS
; ----------------------
;
; SetPosSVD01 | Ordena por i2c al módulo de servomotor que se
; | coloque en la posición establecida por "PosNewSVD01"
; SetStatSVD01 | Ordena por i2c al módulo de servomotor la actualización
; | de su registro especial de estado según el valor de
; | "StatSVD01". Ha de tenerse en cuenta que solo se actualizarán
; | aquellos bits que sean R/W. Los demás serán ignorados.
; SetHDBSVD01 | Ordena por i2c al módulo de servomotor que almacene
; | en su registro HalfDeadBand el valor dado por "HDBSVD01"
list | p=16F876
include | "P16F876.INC"

;Definición de constantes

#define ClockValue | d'9' | ;(100khz) valor para cálculo de vel. I2C que pasará a SSPADD

#define DirSVD01 | b'01111000' | ;Dirección Módulo servomotor (01111000)

;Códigos de registro del módulo SVD01
#define SVD01Stat | d'1' | ;Registro de estado

#define SVD01Posic | d'3' | ;Posición

#define SVD01Temp | d'4' | ;Temperatura

#define SVD01Curr | d'5' | ;Corriente

#define SVD01HDB | d'6' | ;HalfDeadBand

#define SVD01Ver | d'7' | ;Versión del firmware

;Definición de variables

cblock 0x20
MensajeIn | ;Contendrá el dato recibido por I2C del slave
MensajeOut | ;Contendrá el dato a enviar por I2C al slave
DirSlave | ;Dirección del Slave
BkStatus | ;Backup del registro STATUS
BkW | ;Backup W
BDel0 | ;Usada en retardos
BDel1 | ;Usada en retardos
BDel2 | ;Usada en retardos
Pausa | ;Usada en para hacer pausas con subr "HacerTiempo"

;Registros de módulo SVD01
PosActSVD01 | ;Variable de posición actual de servomotor según dato recibido por i2c
PosNewSVD01 | ;Posición que se desea que tenga la servomotor (2 a 253)
StatSVD01 | ;Registro de estado
TempSVD01 | ;Temperatura
CurrSVD01 | ;Corriente
HDBSVD01 | ;HalfDeadBand
VerSVD01 | ;Versión del firmware
endc | ;Fin de definiciones

org | 0
goto | INICIO
org | 5

;-------------------------------------------------------------------------------

INICIO | ;Inicio del cuerpo del programa
banksel TRISA | ;Apunta a banco 1
movlw | b'00011111' | ;Entrada (switches). Solo 5 inferiores
movwf | TRISA | ;
movlw | b'00000000' | ;Salida (Leds)
movwf | TRISB | ;
banksel PORTB | ;Apunta a banco 0
clrf | PORTB | ;Limpia puerto B
clrf | PORTA | ;Limpia puerto A
call | init_i2c_Master | ;Configuración para uso de i2c
clrf | MensajeIn
clrf | MensajeOut
movlw | d'10' | ;Pausa de 10 centésimas de segundo para que en...
movwf | Pausa | ;...el arranque de tiempo a los slaves a quedar...
call | HacerTiempo | ;..configurados adecuadamente.

;********************************************************************************** ;A partir de aquí ha de incluirse el código con el que controlar el servomotor
;El control sobre el servomotor se realizará mediante llamadas a las diferentes ;rutinas de lectura y escritura de registros comentadas al principio del programa. ;**********************************************************************************

MLoop

;Proceso para resetear el slave en caso de bloqueo de algún tipo
call Send_RStart
call Send_Stop
banksel PORTB

;Ordena movimiento a posición concreta
movlw | d'255'
movwf | PosNewSVD01
call | SetPosSVD01

;pausa de 50 centésimas de segundo
movlw | d'50'
movwf | Pausa
call | HacerTiempo

;Lee registro de corriente del módulo servomotor
call | ReadCurrSVD01
movf | CurrSVD01,W
movwf | PORTB | ;muestra en leds de portb

;pausa de 200 centésimas de segundo (2 segundos)
movlw | d'200'
movwf | Pausa
call | HacerTiempo

;Ordena movimiento a posición concreta
movlw | d'0'
movwf | PosNewSVD01
call | SetPosSVD01

;pausa de 200 centésimas de segundo (2 segundos)
movlw | d'200'
movwf | Pausa
call | HacerTiempo

goto MLoop

;********************************************************************************* ; SUBRUTINAS
;*********************************************************************************

;-------------------------------------------------------------------------------
ReadPosSVD01 | ;Obtiene por i2c la posición del módulo de servomotor
;y la deja en la variable "PosActSVD01" ;-------------------------------------------------------------------------------

banksel DirSlave
movlw | DirSVD01
movwf | DirSlave
movlw | SVD01Posic | ;Registro 3 de SVD01
movwf | MensajeOut
call | Send_Start | ;Envía condición de inicio
banksel DirSlave
call | Enviar | ;Envía el dato al Slave
call | Send_RStart | ;Envía condición de reinicio
banksel DirSlave
call | Recibir | ;Toma dato del Slave...
movf | MensajeIn,W | ;...y lo guarda en...
movwf | PosActSVD01 | ;...la variable de registro correspondiente
call | Send_Stop | ;Envía condición de stop
banksel DirSlave

return

;-------------------------------------------------------------------------------
SetPosSVD01 | ;Ordena por i2c al módulo de servomotor que se
;coloque en la posición establecida por "PosNewSVD01" ;-------------------------------------------------------------------------------

banksel DirSlave
movlw | DirSVD01
movwf | DirSlave
movlw | SVD01Posic | ;Registro 3 de SVD01
movwf | MensajeOut
call | Send_Start | ;Envía condición de inicio
banksel DirSlave
call | Enviar | ;Envía el dato al Slave
movf | PosNewSVD01,W ;Se deja en W para que...
call | Send_Byte | ;...Send_Byte lo envíe por i2c
call | Send_Stop | ;Envía condición de stop
banksel DirSlave
return

;-------------------------------------------------------------------------------
ReadTempSVD01 | ;Lee el valor de temperatura del módulo SVD01 y la deja
;en TempSVD01
;-------------------------------------------------------------------------------

;Leemos temperatura en SVD01
banksel DirSlave
movlw | DirSVD01
movwf | DirSlave
movlw | SVD01Temp | ;Registro 4 de SVD01 (Registro de temperatura)
movwf | MensajeOut
call | Send_Start | ;Envía condición de inicio
banksel DirSlave
call | Enviar | ;Envía el dato al Slave
call | Send_RStart | ;Envía condición de reinicio
banksel DirSlave
call | Recibir | ;Toma dato del Slave...
movf | MensajeIn,W | ;...y lo guarda en...

movwf | TempSVD01 | ;...la variable correspondiente
call | Send_Stop | ;Envía condición de stop
banksel DirSlave

return

;-------------------------------------------------------------------------------ReadCurrSVD01 ;Lee el valor de consumo del módulo SVD01
;y lo deja en la variables CurrSVD01 ;-------------------------------------------------------------------------------

banksel DirSlave
movlw | DirSVD01
movwf | DirSlave
movlw | SVD01Curr | ;Registro 5 de SVD01 (Registro de Corriente)
movwf | MensajeOut
call | Send_Start | ;Envía condición de inicio
banksel DirSlave
call | Enviar | ;Envía el dato al Slave
call | Send_RStart | ;Envía condición de reinicio
banksel DirSlave
call | Recibir | ;Toma dato del Slave...
movf | MensajeIn,W | ;...y lo guarda en...
movwf | CurrSVD01 | ;...la variable correspondiente
call | Send_Stop | ;Envía condición de stop
banksel DirSlave

return

;-------------------------------------------------------------------------------
ReadStatSVD01 | ;Lee el registro de estado del módulo SVD01 y lo deja
;en StatSVD01
;-------------------------------------------------------------------------------

;Leemos registro de estado en MD03_1
banksel DirSlave
movlw | DirSVD01
movwf | DirSlave
movlw | SVD01Stat | ;Registro 1 de SVD01 (registro de estado)
movwf | MensajeOut
call | Send_Start | ;Envía condición de inicio
banksel DirSlave
call | Enviar | ;Envía el dato al Slave
call | Send_RStart | ;Envía condición de reinicio
banksel DirSlave
call | Recibir | ;Toma dato del Slave...
movf | MensajeIn,W | ;...y lo guarda en...
movwf | StatSVD01 | ;...la variable de registro correspondiente
call | Send_Stop | ;Envía condición de stop
banksel DirSlave

return

;-------------------------------------------------------------------------------
SetStatSVD01 | ;Ordena por i2c al módulo de servomotor la actualización
;de su registro especial de estado según el valor de ;"StatSVD01". Ha de tenerse en cuenta que solo se actualizarán ;aquellos bits que sean R/W. Los demás serán ignorados. ;-------------------------------------------------------------------------------

banksel DirSlave
movlw | DirSVD01
movwf | DirSlave
movlw | SVD01Stat | ;Registro 1 de SVD01 (Estado)
movwf | MensajeOut
call | Send_Start | ;Envía condición de inicio
banksel DirSlave
call | Enviar | ;Envía el dato al Slave

movf | StatSVD01,W | ;Se deja en W para que...
call | Send_Byte | ;...Send_Byte lo envíe por i2c
call | Send_Stop | ;Envía condición de stop
banksel DirSlave
return

;-------------------------------------------------------------------------------
ReadHDBSVD01 | ;Obtiene por i2c el registro HalfDeadBand del módulo de
;servomotor y la deja en la variable "HDBSVD01" ;-------------------------------------------------------------------------------

banksel DirSlave
movlw | DirSVD01
movwf | DirSlave
movlw | SVD01HDB | ;Registro 6 de SVD01
movwf | MensajeOut
call | Send_Start | ;Envía condición de inicio
banksel DirSlave
call | Enviar | ;Envía el dato al Slave
call | Send_RStart | ;Envía condición de reinicio
banksel DirSlave
call | Recibir | ;Toma dato del Slave...
movf | MensajeIn,W | ;...y lo guarda en...
movwf | HDBSVD01 | ;...la variable de registro correspondiente
call | Send_Stop | ;Envía condición de stop
banksel DirSlave

return

;-------------------------------------------------------------------------------
SetHDBSVD01 | ;Ordena por i2c al módulo de servomotor que almacene
;en su registro HalfDeadBand el valor dado por "HDBSVD01" ;-------------------------------------------------------------------------------

banksel DirSlave
movlw | DirSVD01
movwf | DirSlave
movlw | SVD01HDB | ;Registro 6 de SVD01
movwf | MensajeOut
call | Send_Start | ;Envía condición de inicio
banksel DirSlave
call | Enviar | ;Envía el dato al Slave
movf | HDBSVD01,W | ;Se deja en W para que...
call | Send_Byte | ;...Send_Byte lo envíe por i2c
call | Send_Stop | ;Envía condición de stop
banksel DirSlave
return

;-------------------------------------------------------------------------------
ReadVerSVD01 | ;Obtiene por i2c la versión de firmware del módulo de
;servomotor y la deja en la variable "VerSVD01" ;-------------------------------------------------------------------------------

banksel DirSlave
movlw | DirSVD01
movwf | DirSlave
movlw | SVD01Ver | ;Registro 6 de SVD01
movwf | MensajeOut
call | Send_Start | ;Envía condición de inicio
banksel DirSlave
call | Enviar | ;Envía el dato al Slave
call | Send_RStart | ;Envía condición de reinicio
banksel DirSlave
call | Recibir | ;Toma dato del Slave...
movf | MensajeIn,W | ;...y lo guarda en...
movwf | VerSVD01 | ;...la variable de registro correspondiente
call | Send_Stop | ;Envía condición de stop
banksel DirSlave

return

;-------------------------------------------------------------------------------
init_i2c_Master | ;Inicializa valores para uso de I2C en Master
;Ha de ser llamado tras definir TRISC y un valor para ;ClockValue. Para frecuencia SCL=Fosc/(4x(ClockValue+1)) ;-------------------------------------------------------------------------------

;Guardamos copia de algunos registros
movwf | BkW | ;Hace copia de W
movf | STATUS,W | ;Hace copia de registro de estado
banksel PORTA
movwf BkStatus

;Configuramos I2C
banksel TRISC | ; Pasamos a direccionar Banco 1
movlw | b'00011000' | ; Establece líneas SDA y SCL como entradas...
iorwf | TRISC,f | ;..respetando los valores para otras líneas.
movlw | ClockValue | ; Establece velocidad I2C segun...
movwf | SSPADD | ; ...valor de ClockValue
bcf | SSPSTAT,6 | ; Establece I2C input levels
bcf | SSPSTAT,7 | ; Habilita slew rate
banksel SSPCON | ; Pasamos a direccionar Banco 0
movlw | b'00111000' | ; Master mode, SSP enable, velocidad segun...
movwf | SSPCON | ; ... Fosc/(4x(SSPADD+1))
bcf | PIR1,SSPIF | ; Limpia flag de eventos SSP
bcf | PIR1,7 | ; Limpia bit. Mandatorio por Datasheet

;Restauramos las copias de los registros
movf | BkStatus,W | ;Restaura las copias de registros
movwf | STATUS | ;registro de estado
movf | BkW,W | ;registro W

return

; --------------------------------------------------------------------------------------Enviar ;Envía un mensaje (comando) almacenado en "MensajeOut" al Slave cuya dirección ;se ha de encontrarse en la variable "DirSlave" ;---------------------------------------------------------------------------------------

;Guardamos copia de algunos registros
movwf | BkW | ;Hace copia de W
movf | STATUS,W | ;Hace copia de registro de estado
banksel PORTA
movwf BkStatus

StEnv
banksel DirSlave
movf | DirSlave,W | ;Dirección esclavo
call | Send_Byte | ;Envía dirección y orden de escritura
call | WrtAckTest | ;Verifica llegada ACK
banksel SSPCON2
bcf | SSPCON2,ACKSTAT | ;limpia flag ACK
xorlw | 1
btfss | STATUS,Z | ;Chequea si llegó ACK
goto | SigueEnv | ;Si. Seguimos con envío dato
call | Send_Stop | ;No. Reintentamos envío
call | Send_Start
goto | StEnv

SigueEnv
banksel MensajeOut
movf | MensajeOut,W | ;Lo deja en W para que la subrutina Send_Byte lo envíe
call | Send_Byte | ;envía por i2c

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

return

; --------------------------------------------------------------------------------------Recibir ;Solicita dato al Slave cuya dirección ha de encontrarse en la variable ;"DirSlave" y lo mete en "MensajeIn". ;---------------------------------------------------------------------------------------

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

StRec
banksel DirSlave
movf | DirSlave,W | ;Dirección esclavo
iorlw | b'00000001' | ;con orden de lectura
call | Send_Byte | ;Envía dirección y orden de lectura
call | WrtAckTest | ;Verifica llegada ACK
banksel SSPCON2
bcf | SSPCON2,ACKSTAT | ;limpia flag ACK
xorlw | 1
btfsc | STATUS,Z | ;Chequea si llegó ACK
goto | StRec | ;No. Reintentamos envío
;Si. Leemos dato
call | Rec_Byte | ;Recibe dato por i2c y lo mete en "MensajeIn"

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

return

; --------------------------------------------------------------------------------------Send_Start ;Envía condición de start ;---------------------------------------------------------------------------------------

banksel SSPCON2
bsf | SSPCON2,SEN | ; Envía Start
call | CheckIdle | ;Espera fin evento
return

; --------------------------------------------------------------------------------------Send_RStart ;Envía condición de Repeated Start ;---------------------------------------------------------------------------------------

banksel SSPCON2
bsf | SSPCON2,RSEN | ; Envía Repeated Start
call | CheckIdle | ;Espera fin evento
return

; --------------------------------------------------------------------------------------
Send_Ack | ;Envía Ack
;---------------------------------------------------------------------------------------

banksel SSPCON2
bcf | SSPCON2,ACKDT ; acknowledge bit state to send (ack)
bsf | SSPCON2,ACKEN ; Inicia secuencia de ack
call | CheckIdle | ;Espera fin evento
return

; --------------------------------------------------------------------------------------
Send_Nack | ;Envía Nack para finalizar recepción
;---------------------------------------------------------------------------------------

banksel SSPCON2
bsf | SSPCON2,ACKDT ; acknowledge bit state to send (not ack)
bsf | SSPCON2,ACKEN ; Inicia secuencia de nack
call | CheckIdle | ;Espera fin evento
return

; --------------------------------------------------------------------------------------
Send_Stop | ;Envía condición de stop
;---------------------------------------------------------------------------------------

banksel SSPCON2
bsf | SSPCON2,PEN | ;Activa secuencia de stop
call | CheckIdle | ;Espera fin evento
return

; --------------------------------------------------------------------------------------
Send_Byte | ;Envía el contenido de W por i2c
;---------------------------------------------------------------------------------------
banksel SSPBUF | ; Cambia a banco 0
movwf | SSPBUF | ; inicia condicion de escritura
call | CheckIdle | ;Espera fin evento
return

; --------------------------------------------------------------------------------------
Rec_Byte | ;Recibe dato por i2c y lo mete en "MensajeIn"
;---------------------------------------------------------------------------------------
banksel SSPCON2 | ; Cambia a banco 1
bsf | SSPCON2,RCEN | ; genera receive condition
btfsc | SSPCON2,RCEN | ; espera a que llegue el dato
goto | $-1
banksel SSPBUF | ; Cambia a banco 0
movf | SSPBUF,w | ; Mueve el dato recibido ...
movwf | MensajeIn | ; ... a MensajeIn
call | CheckIdle | ;Espera fin evento
return

; --------------------------------------------------------------------------------------
CheckIdle | ;Chequea que la operación anterior termino y se puede proceder con
;el siguiente evento SSP
;---------------------------------------------------------------------------------------
banksel SSPSTAT | ; Cambia a banco 1
btfsc | SSPSTAT, R_W | ; Transmisión en progreso?
goto | $-1
movf | SSPCON2,W
andlw | 0x1F | ; Chequeamos con mascara para ver si evento en progreso
btfss | STATUS, Z
goto | $-3 | ; Sigue en progreso o bus ocupado. esperamos
banksel PIR1 | ; Cambia a banco 0
bcf | PIR1,SSPIF | ; Limpiamos flag
return

;---------------------------------------------------------------------------------------WrtAckTest ;Chequea ack tras envío de dirección o dato
;Devuelve en W 0 o 1 dependiendo de si llegó (0) o no (1) ACK ;---------------------------------------------------------------------------------------
banksel SSPCON2 | ; Cambia a banco 1
btfss | SSPCON2,ACKSTAT ;Chequea llegada ACK desde slave
retlw | 0 | ;llegó ACK
retlw | 1 | ;no llegó ACK

;---------------------------------------------------------------------------------------HacerTiempo ;realiza una pausa del numero de centesimas de segundo especificadas en "Pausa"

;---------------------------------------------------------------------------------------

movf | Pausa,W | ;Coloca el valor de pausa en BDel2...
movwf | BDel2 | ;...para no alterar su contenido
; |
; Generado con PDEL ver SP r 1.0 el 24/02/03 Hs 18:31:22
; Descripcion: Delay 10000 ciclos (1 centésima de segundo)
; |

BCiclo movlw | .8 | ; 1 set numero de repeticion (B)
movwf | BDel0 | ; 1 |
BLoop1 movlw | .249 | ; 1 set numero de repeticion (A)
movwf | BDel1 | ; 1 |
BLoop2 nop | | ; 1 nop
nop | | ; 1 ciclo delay
decfsz | BDel1, 1 ; 1 + (1) es el tiempo 0 ? (A)
goto | BLoop2 | ; 2 no, loop
decfsz | BDel0, 1 ; 1 + (1) es el tiempo 0 ? (B)
goto | BLoop1 | ; 2 no, loop
BDelL1 goto BDelL2 | ; 2 ciclos delay
BDelL2 nop | | ; 1 ciclo delay
; |
decfsz BDel2,F | ;Repite tantas veces el ciclo de una decima de segundo...
goto | BCiclo | ;..como se lo indique ADel2
return | | ; 2+2 Fin.

END

# Líneas futuras

El modelo de servocontrol presentado permite mejoras considerables, como la reducción de tamaño y sobre todo un control más preciso de la posición del servo mediante la reducción de velocidad al acercarse a la posición seleccionada, con lo que se evitará el balanceo de ajuste que puede acontecer con valores de “HalfDeadBand” bajos y escasa carga.

Indudablemente una evolución de los servomotores de radiocontrol hacia los servomotores I² C
facilitaría enormemente el control de cantidades grandes de servos en sistemas complejos y evitaría el uso inútil de puertos y capacidad de proceso de los microcontroladores master.

Son este tipo de servomotores y no los de radiocontrol los que realmente requiere la robótica. No solo por su facilidad de control y su reducida necesidad de proceso, sino también por la amplia información para control en bucles cerrados que provee.
